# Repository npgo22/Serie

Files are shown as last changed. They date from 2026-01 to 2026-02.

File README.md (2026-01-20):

# Serie
Serie is a basic mainboard built to handle:
1. Insanely high temperatures
2. Insanely high speeds
3. Several axis of movement

The board itself is based around an STM32H723, the fastest microcontroller supported by Klipper at the moment.

## I/O
Currently, the following I/O is planned:

### Temperature sensing
Four MAX31856 (for type-k thermocouples) modules will be integrated for temperature sensing to be used as follows:
1. Hotend
2. Bed
3. Chamber
4. Spare/standby

Several other standard thermistor inputs will be broken out as needed.

### Motors
There will be 6x motors driven by TMC2241s. Each TMC2241 Support to klipper will need to be added to support this.

### Isolated Inputs
There are 16 digitally isolated inputs.

### Low Power Outputs
There are 6 outputs driven by small MOSFETs for outputs to other devices.

### Buses
As many buses should be broken out as possible.

### 12V Outputs
There are four 12V outputs to drive peripherals such as fans.

### USB
There will be at least 1 USB-C input.

### Ethernet
As I have ethernet stuff on hand, this board will have ethernet.

### Piezo Inputs
There will be a transimpedance amplifier followed by an instrumentation amplifier and an external comparator for piezo measurement. This is because the beacon probe cannot handle higher temperatures.

### Endstops
The enstops will utilize optoisolated inputs, and will be 3 pins to accomodate hall effect sensors.

## Power
As of right now, it is planned to require an external 48V power supply for the motors and a 12V power supply for the mainboard. This maintains galvanic isolation while providing decent protection against  A small switching regulator will generate 5V (AP62300TWU-7 + ETQP4M3R3KVK) which will then be fed into a 2112K-3.3.

### Heaters
Bed and chamber will be mains-powered, and motors will see 48V to 60V. and all the fans will maintain 12V, and the hotend heater cartridge will be able to handle 24V but will require a separate power supply just for it.

#### Switching
Mains powered items will be driven by an SSR, which necessitates the selection of a decent gate driver.

### Motors
Motors will be powered by a separate 48V power supply as they are extremely noisy.

## Board construction
Probably 4 layers. Don't really need more at this time.

## Misc.
* Consider a standardized header for breaking out to other boards.
* Total BoM cost for 2x is expected to be in the neighborhood of $150 once it's all assembled.

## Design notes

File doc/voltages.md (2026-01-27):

# Regulators
A set of voltage regulators can be seen on the regulators sheet. They are as follows:

|Regulator|Rail |Purpose|
|---|-----|---|
|AP64500  |+12V |For fans|
|AP64500  |+5V  |For digital +5V peripherals|
|AP2112K  |+3.3V|For low-power 3.3V peripherals|
|TPS7A2 |+4.5V|Specifically for the load cell|

For each of them, a set of 22uF capacitors are used in parallel to lower ESR/ESL and to raise the effective capcitance. The AP64500 uses frequency spread techniques to decrease noise among a few other tricks, which is important for our application. Ripple current is managed by the aforementioned 22uF capacitor sets. 

## AP64500 General
Generally, we do not use the UVLO feature as it adds complexity to the BOM and the case of a brownout doesn't really affect anything. Furthermore, a target switching frequency of 500 kHz is used as is standard to simplify math. This gives us the value for the RT/CLK pin of $200\mathrm{k\Omega}$.

We do not require power sequencing for this application, either, so we just tie EN to VIN.

### AP64500 Math
We already use $10\mathrm{k\Omega}$ resistors elsewhere in the design, so to calculate R1:

$$ R_1 = R_2 \cdot (\frac{V_{out}}{0.8\mathrm{V}} - 1) = 10,000\cdot(\frac{12\mathrm{V}}{0.8\mathrm{V}} - 1) = 140\mathrm{k\Omega}$$
$$ R_1 = R_2 \cdot (\frac{V_{out}}{0.8\mathrm{V}} - 1) = 10,000\cdot(\frac{5\mathrm{V}}{0.8\mathrm{V}} - 1) = 52.5\mathrm{k\Omega}$$

The closest E96 values for these are $140\mathrm{k\Omega}$ exact and $52.3\mathrm{k\Omega}$.

Now for the inductor at the top of our expected input voltage:
$$L = V_{out}\cdot\frac{(V_{in}-V_{out})}{V_{in}\cdot\Delta I_L \cdot f_{sw}} = \frac{12\mathrm{V}\cdot(24\mathrm{V}-12\mathrm{V})}{24\mathrm{V}\cdot2.5\mathrm{A}\cdot500,000} = 4.8\mathrm{\mu H}$$

$$L = V_{out}\cdot\frac{(V_{in}-V_{out})}{V_{in}\cdot\Delta I_L \cdot f_{sw}} = \frac{5\mathrm{V}\cdot(24\mathrm{V}-5\mathrm{V})}{24\mathrm{V}\cdot2.5\mathrm{A}\cdot500,000} = 3.167\mathrm{\mu H}$$

Now we should round up because a standard LED strip power supply can be cranked up in excess of the rated output voltage. As such, we will use inductor values of $6.8\mathrm{\mu H}$ and $3.3\mathrm{\mu H}$ far above our expected carrying current capacity of 5A, respectively.

Now before we go further we have to look at our deratings. For our application, the only reasonably-sized capacitors we can use at this point are 0805 X5R. X7R does not have the required voltage ratings. We will use the data from Samsung's [CL21A226MAYNNN](https://product.samsungsem.com/mlcc/CL21A226MAYNNN.do), which clearly shows a derating of -83% at 12V and -60% at 5V.

So we get:
$$3\cdot22\mathrm{\mu F}\cdot(1-0.83)=11.22\mathrm{\mu F}$$
$$3\cdot22\mathrm{\mu F}\cdot(1-0.6)=26.4\mathrm{\mu F}$$

From here we now need to calculate our values for External Loop Compensation (crossover frequency of $\frac{1}{10}f_{sw}$):

$$R_5=\frac{2\pi\cdot f_c \cdot V_{out} \cdot C_O \cdot R_T}{g_m\cdot V_{FB}}

=4.67\cdot10^3\cdot 50,000 \cdot 12\mathrm{V}\cdot 11.22\mathrm{\mu F} = 31.438\mathrm{k\Omega}$$
and:
$$R_5=\frac{2\pi\cdot f_c \cdot V_{out} \cdot C_O \cdot R_T}{g_m\cdot V_{FB}}

=4.67\cdot10^3\cdot 50,000 \cdot 5\mathrm{V}\cdot 26.4\mathrm{\mu F} = 30,822\mathrm{k\Omega}$$

The capacitor values were then both calculated to be 
$856\mathrm{pF} and 855\mathrm{pF}$, respectively.

This is actually a fairly fortunate coincidence that will allow for BOM consolidation:
Both resistors are going to be $30.9\mathrm{k\Omega}$ and $1\mathrm{nF}$.

Finally, we can calculate our expected output ripple:

$$V_{ripple} = \Delta I_L \cdot (\mathrm{ESR} + \frac{1}{8\cdot f_{sw} \cdot C_{OUT}}) $$

Which comes out to (assuming ESR is $0.67\mathrm{m\Omega}$ since it's $2\mathrm{m\Omega}$ for a single resistor) $40.4\mathrm{mV}$ for the +12V rail total and $22.7\mathrm{mV}$ for the +5V rail.

This is super low, and our only real concern is output transients causing the rail to sag, however this is irrelevant on both rails (+5V draws little current, +12V is just fans).

## LDOs
For both, we just used a handfull of input and output capacitors to minimize ripple. The LDOs used have really good high-frequency PSRRs, so we don't really worry about any sort of filtering past this. 

For USB power, only the main USB power is considered. This is just to simplify power plane management, and the scenarios wherein you would only have 1 USB port available are far and few between.

A diode is applied on the 5V regulator's output to prevent backflow when external USB power is supplied.

The +4.5V regulator was chosen in accordance with the minimum USB voltage of +4.8V minus the dropout.

### Expected ripple
From above we got the output ripple from our +5V regulator which feeds our LDOs. This came out to $22.7\mathrm{mV}$. If we estimate the PSRR (each eyeballed from the datasheets graphs) for the AP2112K to be 25dB and 55dB for the TPS7A20 at 500kHz, we can do some log math to derive the HF attenuation will be 17.8x for the AP2112K and 562x for the TPS7A20. This means our ripple is projected to be around 0.08mV and 1.65mV, respectively. These figures are more tha suitable for our purposes. With figures so good, it is meaningless to add more filtering, and in fact adding more will worsen performance as it will most certainly cause resonances.

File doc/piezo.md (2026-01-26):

# Piezo Circuit
This board integrates a simple charge amplifier followed by a discrete two-stage PGA followed by a comparator to achieve a fairly sensitive high-temperature piezo trigger circuit. We are aiming to measure down to 0.005N with a standard PZT-5A piezo as a stretch goal.

The circuit itself consists of a charge amplifier feeding into a noninverting discrete programmable gain amplifier followed by a voltage follower to prevent output loading. In addition, the last available opamp channel is used to generate a virtual ground.

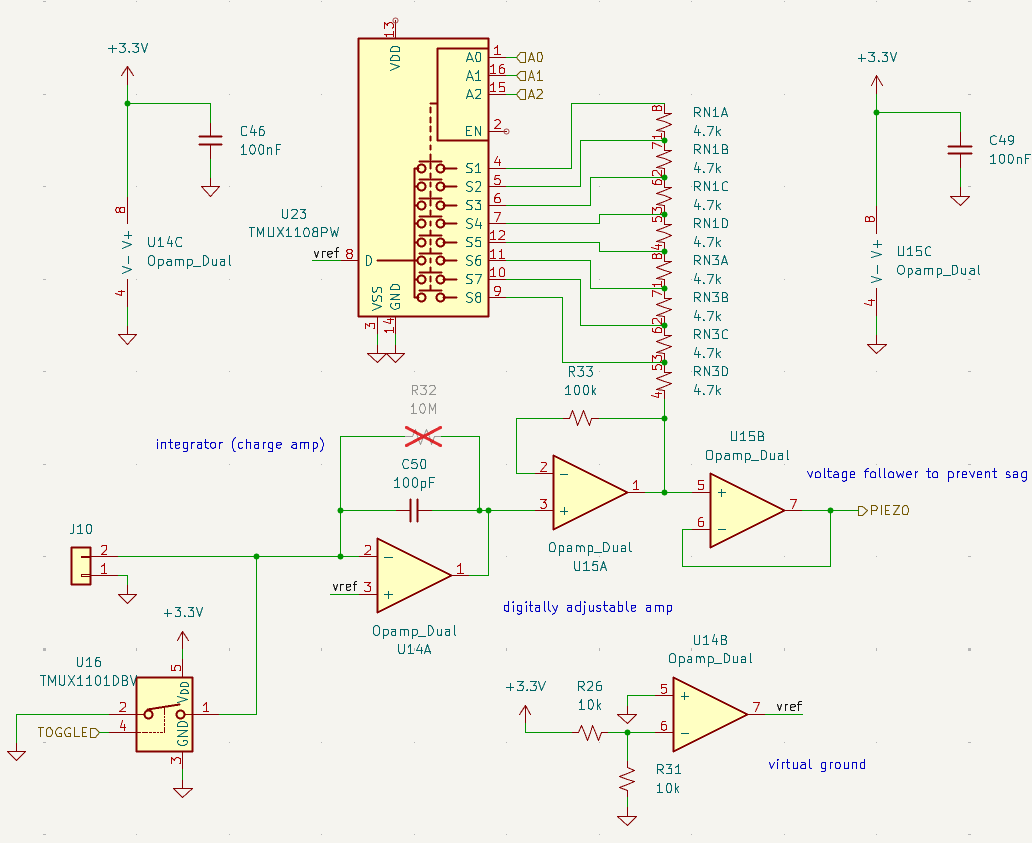
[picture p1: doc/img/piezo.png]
An incomplete picture of the piezo circuit Incomplete circuit


## Charge Amplifier
Here we needed the signal to be significant enough to not be consumed by noise. As a PZT-5A piezo has a $d_{33} = 390\cdot 10^{-12} \mathrm{\frac{C}{N}}$, we went with a capacitor value of ${100\mathrm{pF}}$ such that:
$$ V_{charge} = \frac{390\cdot10^{-12} \mathrm{\frac{C}{N}} \cdot 0.005\mathrm{N}}{100\cdot 10^{-12}} = 19.5\mathrm{mV}$$

At the top our range, this comes out to:
$$ V_{charge} = \frac{390\cdot10^{-12} \mathrm{\frac{C}{N}} \cdot 0.1\mathrm{N}}{100\cdot 10^{-12}} = 390\mathrm{mV}$$

Both of these values are very usable for our purposes.

## Non-Inverting Amplifier
The gain of a non-inverting amplifier is: $$G = 1+\frac{R_F}{R_2}$$
From this, we just plug in our values to achieve:
$$G = 1+\frac{100,000\Omega}{n\cdot4,700\Omega}$$
Where $n$ is the active amount of resistors in our resistor ladder as seen on the mux.
From this, we get the folowing table:
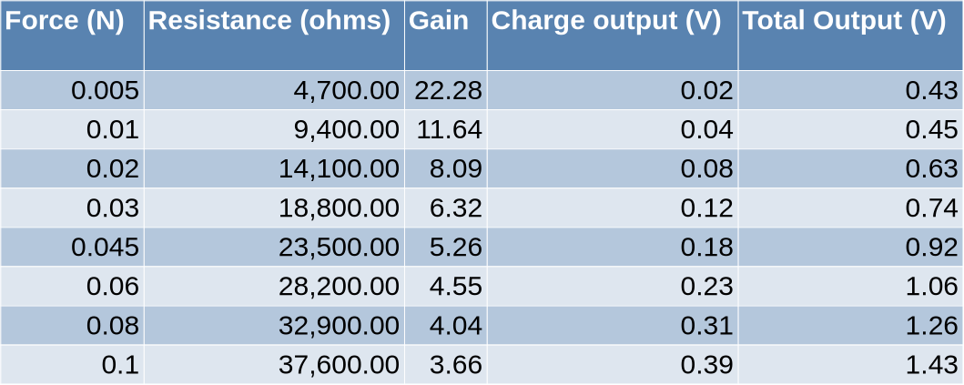
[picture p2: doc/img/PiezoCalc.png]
Piezo calculations Piezo Calculations


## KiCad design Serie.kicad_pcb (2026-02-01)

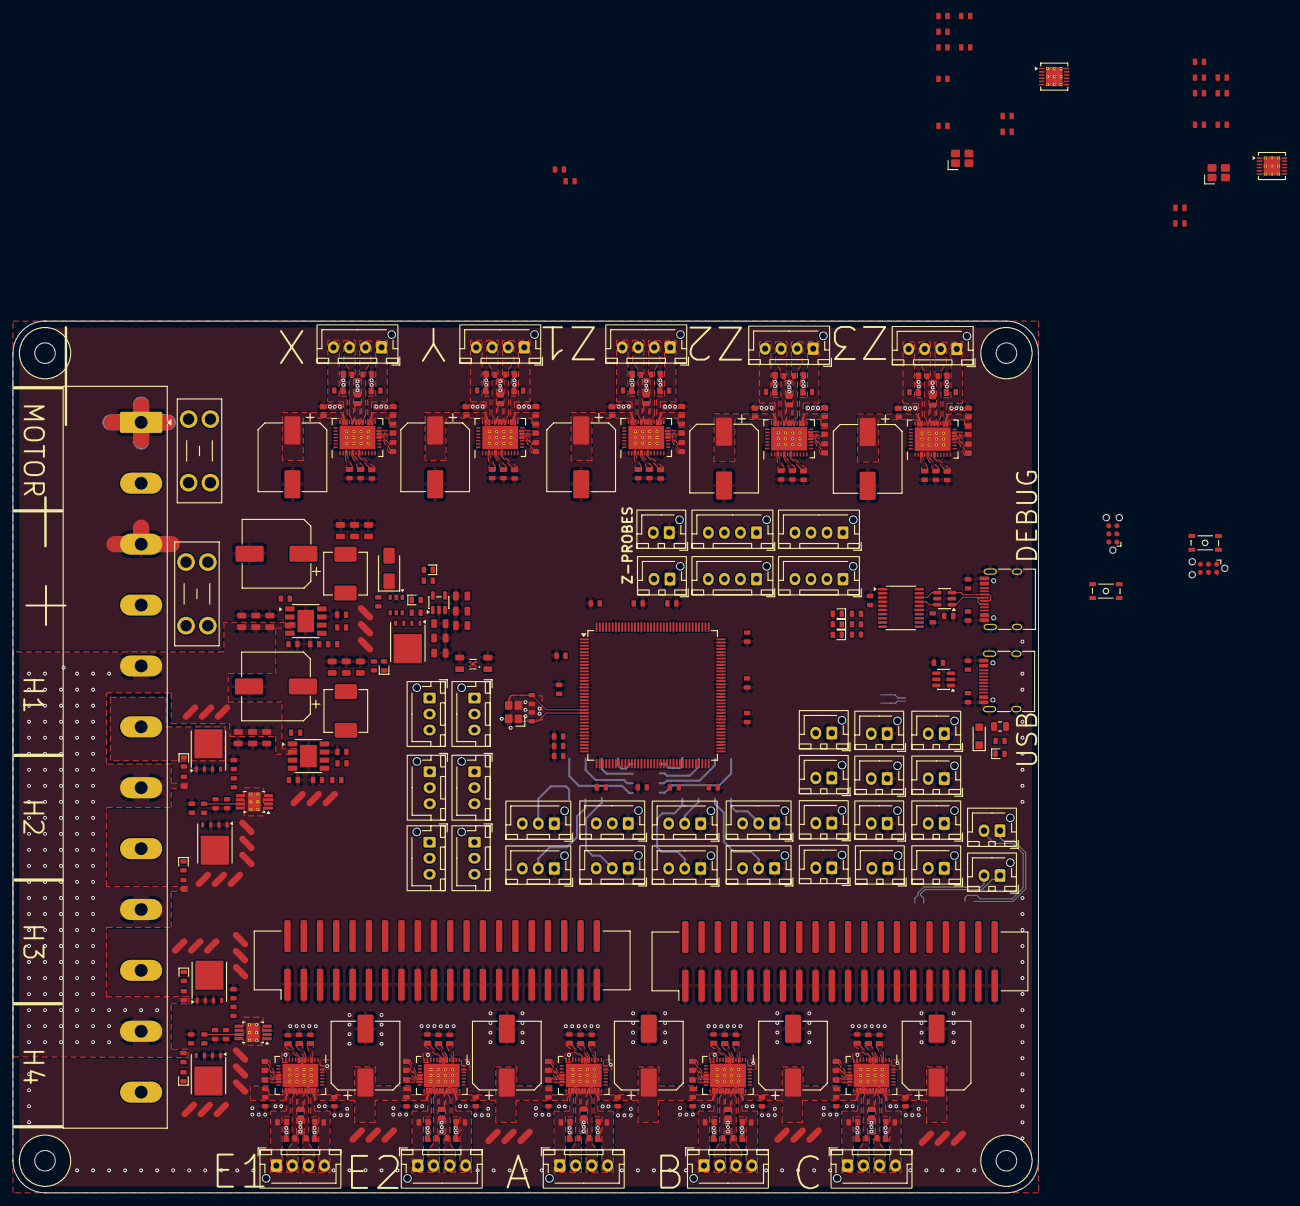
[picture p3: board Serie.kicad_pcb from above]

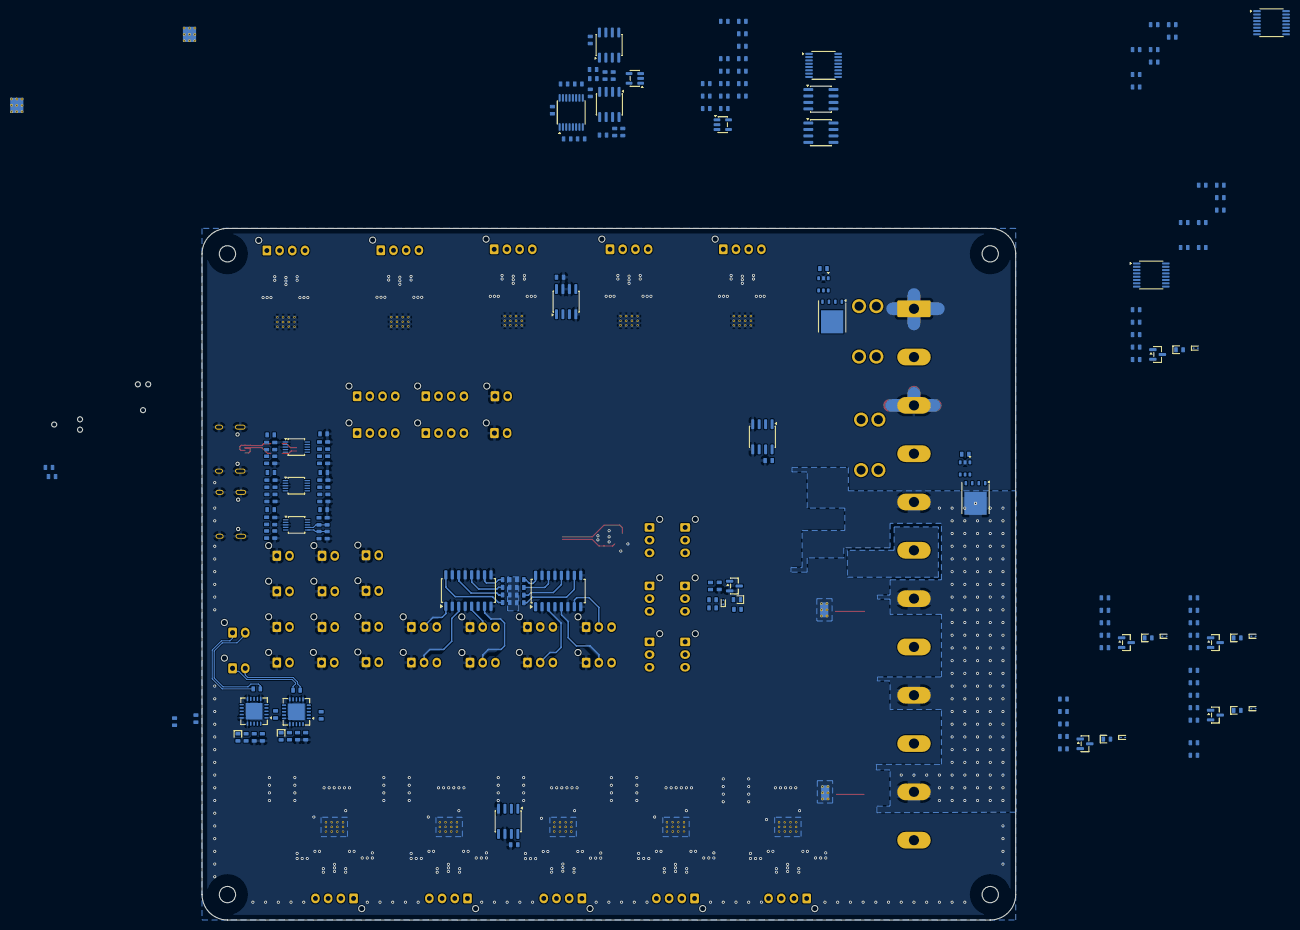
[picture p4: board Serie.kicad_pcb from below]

Board: 6 copper layers, 160.0 x 136.0 mm, 518 parts (179 on the bottom side), 303 nets.

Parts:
C1, C2: 10pF; C_0603
C3, C4, C93, C105, C117, C129, C141, C153, C184, C214, C226, C238: 2.2uF; C_0603
C5, C6, C7, C9, C12, C13, C14, C18, C19, C20, C21, C22, C24, C25, C26, C27, C28, C36, C38, C46, C56, C58, C59, C60, C61, C62, C63, C64, C65, C66, C67, C68, C69, C70, C71, C72, C74, C76, C77, C79, C80, C84, C85, C86, C92, C96, C97, C98, C104, C108, C109, C110, C116, C120, C121, C122, C128, C132, C133, C134, C140, C144, C145, C146, C152, C154, C155, C156, C158, C161, C162, C163, C167, C168, C169, C170, C171, C175, C176, C177, C183, C185, C186, C187, C188, C189, C191, C192, C193, C194, C195, C197, C198, C199, C200, C201, C205, C206, C207, C213, C217, C218, C219, C225, C229, C230, C231, C237: 100nF; C_0603
C8, C11, C78, C81, C157, C160: 10nF; C_0603
C10, C159: 10uF; C_0603
C15, C16, C164, C165: ?uF; C_0603
C17, C166: 100pF; C_0603
C23, C172: 30pF; C_0603
C29, C30, C31, C33, C34, C35, C39, C40, C41, C43, C44, C45, C48, C49, C50, C51, C52, C53, C54, C55: 22uF; C_0805
C32, C42, C87, C99, C111, C123, C135, C147, C178, C208, C220, C232: 100uF; CP_Elec_10x10.5
C37, C47: 1nF; C_0603
C57, C73, C75: 1uF; C_0603
C82, C83, C94, C95, C106, C107, C118, C119, C130, C131, C142, C143, C173, C174, C203, C204, C215, C216, C227, C228: 22nF; C_0603
C88, C89, C90, C91, C100, C101, C102, C103, C112, C113, C114, C115, C124, C125, C126, C127, C136, C137, C138, C139, C148, C149, C150, C151, C179, C180, C181, C182, C209, C210, C211, C212, C221, C222, C223, C224, C233, C234, C235, C236: 470pF; C_0603
C190, C196, C202: 100n; C_0603
D1: PMEG3010BER; Nexperia_CFP3_SOD-123W
D2, D3, D4, D5, D6, D8, D9, D10, D11, D12, D13, D14, D16, D18, D22, D24, D26: LED_Small; LED_0603
D7: SS54; D_SMA
D15, D17, D19, D23, D25, D27: ESD9B3.3ST5G; D_SOD-923
D20, D21: LED; LED_0603
F1: 500mA; Fuse_0805_2012Metric
F2, F3: XF-508P-B-B; Fuseholder_Blade_Mini_Keystone_3568
H1, H2, H3, H4: MountingHole; MountingHole_3.2mm_M3
J1, J2: Conn_02x20_Counter_Clockwise; IDC-Header_2x20_P2.54mm_Vertical_SMD
J3, J9: Conn_ARM_SWD_TagConnect_TC2030-NL; Tag-Connect_TC2030-IDC-NL_2x03_P1.27mm_Vertical
J4, J5, J24, J25, J26, J27, J28, J29, J30, J31, J33, J46, J47, J48: Conn_01x04; JST_XH_B4B-XH-AM_1x04_P2.50mm_Vertical
J6, J22, J23, J32, J34, J35, J36, J37, J38, J39, J40, J41, J42, J43, J44, J45: Conn_01x02; JST_XH_B2B-XH-AM_1x02_P2.50mm_Vertical
J7, J8: USB_C_Receptacle_USB2.0_16P; USB_C_Receptacle_HRO_TYPE-C-31-M-12
J10: Screw_Terminal_06x01x02; TerminalBlock_Ningbo-Kagnex_HB9500M_1x12_P9.5mm
J11, J12, J13, J14, J15, J16, J17, J18, J19, J20, J21, J49, J50, J51: Conn_01x03; JST_XH_B3B-XH-AM_1x03_P2.50mm_Vertical
L1: 6.8 uH; L_Changjiang_FXL0630
L2: 3.3 uH; L_Changjiang_FXL0630
Q1, Q2, Q3, Q4, Q5, Q6, Q7: BSC016N06NS; TDSON-8-1
Q8, Q9, Q10, Q11, Q12, Q13: AO3400A; SOT-23
R1, R2, R81, R82: 100R; R_0603
R3, R4, R5, R6, R7, R8, R9, R10, R16, R17, R21, R22, R48, R53, R58, R83, R84, R85, R86, R87, R88, R89, R90, R96, R97, R98, R99, R103, R104, R105, R106, R108, R109, R110, R111, R118, R123, R128: 4.7k; R_0603
R11, R36, R39, R42, R45, R50, R55, R60, R91, R120, R125, R130: 100k; R_0603
R12, R92: 10M; R_0603
R13, R14, R15, R18, R19, R20, R23, R25, R28, R31, R33, R34, R37, R40, R43, R46, R47, R51, R52, R56, R57, R61, R62, R63, R64, R65, R66, R67, R68, R69, R70, R72, R73, R93, R94, R100, R101, R102, R107, R112, R116, R117, R121, R122, R126, R127: 10k; R_0603
R24: 140k; R_0603
R26, R30: 200k; R_0603
R27, R32: 30.9k; R_0603
R29: 52.5k; R_0603
R35, R38, R41, R44, R49, R54, R59, R119, R124, R129: 10R; R_0603
R71, R74: 4.02k; R_0603
R75, R76, R77, R78, R79, R80, R95, R113, R114, R115: 24k; R_0603
SW1, SW2: SKRPANE010
U1: STM32H723ZGT6; LQFP-144_20x20mm_P0.5mm
U2, U30: ADS1220xPW; TSSOP-16_4.4x5mm_P0.65mm
U3, U31: TMUX1108PW; TSSOP-16_4.4x5mm_P0.65mm
U4, U5, U32, U33: TLV6742; SOIC-8_3.9x4.9mm_P1.27mm
U6, U34: LDC1612; WSON-12-1EP_4x4mm_P0.5mm_EP2.6x3mm_ThermalVias
U7, U35: TMUX1101DBV; SOT-23-5
U8, U10: USBLC6-2SC6; SOT-23-6
U9: STM32F042F4Px; TSSOP-20_4.4x6.5mm_P0.65mm
U11, U13: AP64500; Diodes_SO-8EP
U12, U14, U17: AP74700Q; SOT-6
U15: TLV77533; SOT-23-5
U16: TPS7A20xxxDQN; Texas_X2SON-4_1x1mm_P0.65mm
U18, U19: UCC27524DGN; Texas_DGN0008G_VSSOP-8-1EP_3x3mm_P0.65mm_EP2x2.94mm_Mask1.8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
U20, U21: LTV-247; SOP-16_4.4x10.4mm_P1.27mm
U22, U23: MAX31865xTP; TQFN-20-1EP_5x5mm_P0.65mm_EP3.25x3.25mm
U24, U25, U26, U27, U28, U29, U36, U43, U44, U45: TMC2241ATC; QFN-38_EP_5.63x7.6_Pitch0.5mm
U37, U39, U42: ADS1115IDGS; TSSOP-10_3x3mm_P0.5mm
U38, U40, U41: LM75B; SOIC-8_3.9x4.9mm_P1.27mm
Y1: 25 MHz; 3225-4P-L
Y2, Y3: 12 MHz; 3225-4P-L

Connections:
+3.3V: C5.2, C7.2, C12.2, C13.2, C14.1, C22.1, C24.1, C25.1, C51.2, C52.2, C53.2, C57.2, C58.2, C59.2, C60.2, C61.2, C62.2, C63.2, C64.2, C65.2, C66.2, C67.2, C68.2, C69.2, C70.2, C71.2, C76.1, C77.1, C79.1, C80.1, C92.2, C104.2, C116.2, C128.2, C140.2, C152.2, C154.2, C156.2, C161.2, C162.2, C163.1, C171.1, C183.2, C185.1, C186.1, C191.1, C192.1, C197.1, C198.1, C213.2, C225.2, C237.2, D3.2 (A), D4.2 (A), D5.2 (A), J3.1 (VCC), J9.1 (VCC), J14.3, J15.3, J16.3, J17.3, J18.3, J19.3, J20.3, J21.3, R13.1, R33.1, R46.1, R51.1, R56.1, R61.1, R62.1, R63.1, R64.1, R65.1, R66.1, R67.1, R68.1, R69.1, R70.1, R72.1, R73.1, R93.1, R96.1, R97.1, R98.1, R99.1, R100.2, R101.2, R102.2, R103.1, R104.1, R105.1, R106.1, R107.2, R108.1, R109.1, R110.1, R111.1, R112.2, R116.1, R121.1, R126.1, U1.6 (VBAT), U1.17 (VDD), U1.30 (VDD), U1.32 (VREF+), U1.33 (VDDA), U1.39 (VDD), U1.52 (VDD), U1.62 (VDD), U1.72 (VDD), U1.84 (VDD), U1.95 (VDD33USB), U1.108 (VDD), U1.121 (VDD), U1.131 (VDD), U1.143 (PDR_ON), U1.144 (VDD), U2.13 (DVDD), U3.2 (EN), U3.13 (VDD), U4.8 (V+), U5.8 (V+), U6.7 (VDD), U7.5 (V_{DD}), U9.5 (VDDA), U9.16 (VDD), U15.5 (VOUT), U22.19 (DVDD), U22.20 (VDD), U23.19 (DVDD), U23.20 (VDD), U24.7 (VCCIO), U24.33 (~SLEEP), U25.7 (VCCIO), U25.33 (~SLEEP), U26.7 (VCCIO), U26.33 (~SLEEP), U27.7 (VCCIO), U27.33 (~SLEEP), U28.7 (VCCIO), U28.33 (~SLEEP), U29.7 (VCCIO), U29.33 (~SLEEP), U30.13 (DVDD), U31.2 (EN), U31.13 (VDD), U32.8 (V+), U33.8 (V+), U34.7 (VDD), U35.5 (V_{DD}), U36.7 (VCCIO), U36.33 (~SLEEP), U37.8 (VDD), U38.6 (A1), U38.7 (A0), U38.8 (+Vs), U39.1 (ADDR), U39.8 (VDD), U40.5 (A2), U40.8 (+Vs), U41.5 (A2), U41.7 (A0), U41.8 (+Vs), U42.8 (VDD), U43.7 (VCCIO), U43.33 (~SLEEP), U44.7 (VCCIO), U44.33 (~SLEEP), U45.7 (VCCIO), U45.33 (~SLEEP), Y2.4 (V+), Y3.4 (V+)
+4.5V: C6.1, C10.1, C55.1, C155.1, C159.1, J4.4, J30.4, U2.11 (AIN0/REFP1), U2.12 (AVDD), U16.1 (OUT), U30.11 (AIN0/REFP1), U30.12 (AVDD)
+5V: C48.2, C49.2, C50.2, C54.1, D1.1 (K), Q2.5 (D), U14.4 (CATHODE), U15.1 (VIN), U15.3 (EN), U16.3 (EN), U16.4 (IN)
+12V: C32.1, C33.1, C34.1, C35.1, C72.2, C73.2, C74.2, C75.2, J11.1, J12.1, J13.1, J49.1, J50.1, J51.1, L1.2, R23.1, R24.1, R47.1, R52.1, R57.1, R117.1, R122.1, R127.1, U18.1 (ENA), U18.6 (V_{DD}), U18.8 (ENB), U19.1 (ENA), U19.6 (V_{DD}), U19.8 (ENB)
+24V: C29.1, C30.1, C31.1, C39.1, C40.1, C41.1, J10.5 (Pin_1), J10.7 (Pin_1), J10.9 (Pin_1), J10.11 (Pin_1), Q1.5 (D), R34.1, R37.1, R40.1, R43.1, U11.2 (VIN), U11.3 (EN), U12.4 (CATHODE), U13.2 (VIN), U13.3 (EN)
/Connections/Debugger and USB/IF_SWCLK: J9.4 (SWCLK), U9.20 (PA14)
/Connections/Debugger and USB/IF_SWDIO: J9.2 (SWDIO), U9.19 (PA13)
/Connections/Debugger and USB/USB_CONN_D+: J7.A6 (D+), J7.B6 (D+), J8.A6 (D+), J8.B6 (D+), U8.3 (I/O2), U10.3 (I/O2)
/Connections/Debugger and USB/USB_CONN_D-: J7.A7 (D-), J7.B7 (D-), J8.A7 (D-), J8.B7 (D-), U8.1 (I/O1), U10.1 (I/O1)
/Connections/Debugger and USB/USB_D+: U9.18 (PA10/PA12), U10.4 (I/O2)
/Connections/Debugger and USB/USB_D-: U9.17 (PA9/PA11), U10.6 (I/O1)
/Connections/Debugger and USB/~RST: J9.3 (~RESET), SW2.3 (K), SW2.4 (A), U9.4 (NRST)
/Connections/High Power Outputs 1/OUTA: R35.1, U18.5 (OUTB)
/Connections/High Power Outputs 1/OUTB: R38.1, U18.7 (OUTA)
/Connections/High Power Outputs 2/OUTA: R41.1, U19.5 (OUTB)
/Connections/High Power Outputs 2/OUTB: R44.1, U19.7 (OUTA)
/Connections/IN1: R61.2, U20.16
/Connections/IN2: R62.2, U20.14
/Connections/IN3: R63.2, U20.12
/Connections/IN4: R64.2, U20.10
/Connections/IN5: R65.2, U21.16
/Connections/IN6: R66.2, U21.14
/Connections/IN7: R67.2, U21.12
/Connections/IN8: R68.2, U21.10
/Connections/Low Power Outputs/TACH1: D15.2 (A2), R46.2, R48.2
/Connections/Low Power Outputs/TACH2: D17.2 (A2), R51.2, R53.2
/Connections/Low Power Outputs/TACH3: D19.2 (A2), R56.2, R58.2
/Connections/Low Power Outputs/TACH4: D23.2 (A2), R116.2, R118.2
/Connections/Low Power Outputs/TACH5: D25.2 (A2), R121.2, R123.2
/Connections/Low Power Outputs/TACH6: D27.2 (A2), R126.2, R128.2
/Connections/SWCLK: J3.4 (SWCLK), U1.109 (PA14(JTCK), U9.12 (PA6)
/Connections/SWDIO: J3.2 (SWDIO), U1.105 (PA13(JTMS), U9.11 (PA5)
/Connections/Sensors 1/CLK: C23.1, U6.3 (CLKIN), Y2.3 (OUT)
/Connections/Sensors 1/PIEZO: U5.6 (-), U5.7
/Connections/Sensors 1/vref: U3.8 (D), U4.3 (+), U4.7
/Connections/Sensors 2/CLK: C172.1, U34.3 (CLKIN), Y3.3 (OUT)
/Connections/Sensors 2/PIEZO: U33.6 (-), U33.7
/Connections/Sensors 2/vref: U31.8 (D), U32.3 (+), U32.7
/Connections/Thermistors/SCL: R101.1, U37.10 (SCL), U38.2 (SCL), U39.10 (SCL), U40.2 (SCL), U41.2 (SCL), U42.10 (SCL)
/Connections/Thermistors/SDA: R102.1, U37.9 (SDA), U38.1 (SDA), U39.9 (SDA), U40.1 (SDA), U41.1 (SDA), U42.1 (ADDR), U42.9 (SDA)
/Connections/Thermistors/TS_ALRT/RDY_1: R100.1, U37.2 (ALERT/RDY)
/Connections/Thermistors/TS_ALRT/RDY_2: R107.1, U39.2 (ALERT/RDY)
/Connections/Thermistors/TS_ALRT/RDY_3: R112.1, U42.2 (ALERT/RDY)
/Connections/Thermocouple 1/T1+: C78.1, J22.2, U22.5 (FORCE+), U22.7 (RTDIN+)
/Connections/Thermocouple 1/T1-: C78.2, J22.1, U22.8 (RTDIN-), U22.9 (FORCE-)
/Connections/Thermocouple 2/T1+: C81.1, J23.2, U23.5 (FORCE+), U23.7 (RTDIN+)
/Connections/Thermocouple 2/T1-: C81.2, J23.1, U23.8 (RTDIN-), U23.9 (FORCE-)
/Connections/~RST: J3.3 (~RESET), SW1.1, SW1.2, U1.25 (NRST), U9.14 (PB1)
/Connections/~TC_CS_1: R70.2, U22.13 (~CS)
/Connections/~TC_CS_2: R73.2, U23.13 (~CS)
DRV_MISO: U24.37 (SDO/NAO), U25.37 (SDO/NAO), U26.37 (SDO/NAO), U27.37 (SDO/NAO), U28.37 (SDO/NAO), U29.37 (SDO/NAO), U36.37 (SDO/NAO), U43.37 (SDO/NAO), U44.37 (SDO/NAO), U45.37 (SDO/NAO)
DRV_MOSI: U24.36 (SDI/AD0), U25.36 (SDI/AD0), U26.36 (SDI/AD0), U27.36 (SDI/AD0), U28.36 (SDI/AD0), U29.36 (SDI/AD0), U36.36 (SDI/AD0), U43.36 (SDI/AD0), U44.36 (SDI/AD0), U45.36 (SDI/AD0)
DRV_SCK: U24.35 (SCK/AD1), U25.35 (SCK/AD1), U26.35 (SCK/AD1), U27.35 (SCK/AD1), U28.35 (SCK/AD1), U29.35 (SCK/AD1), U36.35 (SCK/AD1), U43.35 (SCK/AD1), U44.35 (SCK/AD1), U45.35 (SCK/AD1)
GND: C1.1, C2.1, C3.1, C4.1, C5.1, C6.2, C7.1, C8.1, C11.2, C12.1, C13.1, C14.2, C18.1, C19.1, C20.1, C21.1, C22.2, C23.2, C24.2, C25.2, C26.2, C27.2, C29.2, C30.2, C31.2, C32.2, C33.2, C34.2, C35.2, C37.2, C39.2, C40.2, C41.2, C42.2, C43.2, C44.2, C45.2, C47.2, C48.1, C49.1, C50.1, C51.1, C52.1, C53.1, C54.2, C55.2, C57.1, C58.1, C59.1, C60.1, C61.1, C62.1, C63.1, C64.1, C65.1, C66.1, C67.1, C68.1, C69.1, C70.1, C71.1, C72.1, C73.1, C74.1, C75.1, C76.2, C77.2, C79.2, C80.2, C84.2, C85.2, C86.2, C87.2, C88.2, C89.2, C90.2, C91.2, C92.1, C93.1, C96.2, C97.2, C98.2, C99.2, C100.2, C101.2, C102.2, C103.2, C104.1, C105.1, C108.2, C109.2, C110.2, C111.2, C112.2, C113.2, C114.2, C115.2, C116.1, C117.1, C120.2, C121.2, C122.2, C123.2, C124.2, C125.2, C126.2, C127.2, C128.1, C129.1, C132.2, C133.2, C134.2, C135.2, C136.2, C137.2, C138.2, C139.2, C140.1, C141.1, C144.2, C145.2, C146.2, C147.2, C148.2, C149.2, C150.2, C151.2, C152.1, C153.1, C154.1, C155.2, C156.1, C157.1, C160.2, C161.1, C162.1, C163.2, C167.1, C168.1, C169.1, C170.1, C171.2, C172.2, C175.2, C176.2, C177.2, C178.2, C179.2, C180.2, C181.2, C182.2, C183.1, C184.1, C185.2, C186.2, C187.1, C188.1, C189.1, C190.1, C191.2, C192.2, C193.1, C194.1, C195.1, C196.1, C197.2, C198.2, C199.1, C200.1, C201.1, C202.1, C205.2, C206.2, C207.2, C208.2, C209.2, C210.2, C211.2, C212.2, C213.1, C214.1, C217.2, C218.2, C219.2, C220.2, C221.2, C222.2, C223.2, C224.2, C225.1, C226.1, C229.2, C230.2, C231.2, C232.2, C233.2, C234.2, C235.2, C236.2, C237.1, C238.1, D2.1 (K), D6.1 (K), D8.1 (K), D9.1 (K), D15.1 (A1), D17.1 (A1), D19.1 (A1), D23.1 (A1), D25.1 (A1), D27.1 (A1), J1.1, J1.3, J1.5, J1.7, J1.9, J1.11, J1.13, J1.15, J1.17, J1.19, J1.21, J1.23, J1.25, J1.27, J1.29, J1.31, J1.33, J1.35, J1.37, J1.39, J2.1, J2.3, J2.5, J2.7, J2.9, J2.11, J2.13, J2.15, J2.17, J2.19, J2.21, J2.23, J2.25, J2.27, J2.29, J2.31, J2.33, J2.35, J2.37, J2.39, J3.5 (GND), J6.1, J7.A1 (GND), J7.A12 (GND), J7.B1 (GND), J7.B12 (GND), J7.S1 (SHIELD), J8.A1 (GND), J8.A12 (GND), J8.B1 (GND), J8.B12 (GND), J8.S1 (SHIELD), J9.5 (GND), J10.1, J10.3 (Pin_1), J14.1, J15.1, J16.1, J17.1, J18.1, J19.1, J20.1, J21.1, J32.1, J34.1, J35.1, J36.1, J37.1, J38.1, J39.1, J40.1, J41.1, J42.1, J43.1, J44.1, J45.1, Q4.1 (S), Q4.2 (S), Q4.3 (S), Q5.1 (S), Q5.2 (S), Q5.3 (S), Q6.1 (S), Q6.2 (S), Q6.3 (S), Q7.1 (S), Q7.2 (S), Q7.3 (S), Q8.2 (S), Q9.2 (S), Q10.2 (S), Q11.2 (S), Q12.2 (S), Q13.2 (S), R14.1, R16.1, R17.2, R21.1, R22.2, R25.2, R26.2, R30.2, R31.2, R36.1, R39.1, R42.1, R45.1, R50.1, R55.1, R60.1, R75.2, R76.2, R77.2, R78.2, R79.2, R80.2, R94.1, R95.2, R113.2, R114.2, R115.2, R120.1, R125.1, R130.1, SW1.3 (K), SW1.4 (A), SW2.1, SW2.2, U1.16 (VSS), U1.31 (VSSA), U1.38 (VSS), U1.51 (VSS), U1.61 (VSS), U1.83 (VSS), U1.94 (VSS), U1.107 (VSS), U1.120 (VSS), U1.130 (VSS), U1.138 (BOOT0), U2.3 (CLK), U2.4 (DGND), U2.5 (AVSS), U3.3 (VSS), U3.14 (GND), U4.4 (V-), U4.5 (+), U5.4 (V-), U6.4 (ADDR), U6.6 (SD), U6.8 (GND), U6.13 (GND), U7.2, U7.3 (GND), U8.2 (GND), U9.1 (PB8), U9.15 (VSSA), U10.2 (GND), U11.7 (GND), U11.9 (EP), U12.2 (GND), U13.7 (GND), U13.9 (EP), U14.2 (GND), U15.2 (GND), U16.2 (GND), U16.5 (Pad), U17.2 (GND), U18.3 (GND), U18.9 (GND), U19.3 (GND), U19.9 (GND), U20.2, U20.4, U20.6, U20.8, U20.9, U20.11, U20.13, U20.15, U21.2, U21.4, U21.6, U21.8, U21.9, U21.11, U21.13, U21.15, U22.6 (FORCE2), U22.10 (GND), U22.15 (DGND), U22.16 (GND), U22.21 (GND), U23.6 (FORCE2), U23.10 (GND), U23.15 (DGND), U23.16 (GND), U23.21 (GND), U24.6 (AGND), U24.11 (DRV_EN), U24.23 (PGND), U24.28 (PGND), U24.38 (CLK), U24.39 (EP), U25.6 (AGND), U25.11 (DRV_EN), U25.23 (PGND), U25.28 (PGND), U25.38 (CLK), U25.39 (EP), U26.6 (AGND), U26.11 (DRV_EN), U26.23 (PGND), U26.28 (PGND), U26.38 (CLK), U26.39 (EP), U27.6 (AGND), U27.11 (DRV_EN), U27.23 (PGND), U27.28 (PGND), U27.38 (CLK), U27.39 (EP), U28.6 (AGND), U28.11 (DRV_EN), U28.23 (PGND), U28.28 (PGND), U28.38 (CLK), U28.39 (EP), U29.6 (AGND), U29.11 (DRV_EN), U29.23 (PGND), U29.28 (PGND), U29.38 (CLK), U29.39 (EP), U30.3 (CLK), U30.4 (DGND), U30.5 (AVSS), U31.3 (VSS), U31.14 (GND), U32.4 (V-), U32.5 (+), U33.4 (V-), U34.4 (ADDR), U34.6 (SD), U34.8 (GND), U34.13 (GND), U35.2, U35.3 (GND), U36.6 (AGND), U36.11 (DRV_EN), U36.23 (PGND), U36.28 (PGND), U36.38 (CLK), U36.39 (EP), U37.1 (ADDR), U37.3 (GND), U38.4 (GND), U38.5 (A2), U39.3 (GND), U40.4 (GND), U40.6 (A1), U40.7 (A0), U41.4 (GND), U41.6 (A1), U42.3 (GND), U43.6 (AGND), U43.11 (DRV_EN), U43.23 (PGND), U43.28 (PGND), U43.38 (CLK), U43.39 (EP), U44.6 (AGND), U44.11 (DRV_EN), U44.23 (PGND), U44.28 (PGND), U44.38 (CLK), U44.39 (EP), U45.6 (AGND), U45.11 (DRV_EN), U45.23 (PGND), U45.28 (PGND), U45.38 (CLK), U45.39 (EP), Y1.2 (G), Y1.4 (G), Y2.2 (GND), Y3.2 (GND)
MCU_USB_D+: U1.104 (PA12), U8.4 (I/O2)
MCU_USB_D-: U1.103 (PA11), U8.6 (I/O1)
unnamed: C3.2, U1.71 (VCAP)
unnamed: C4.2, U1.106 (VCAP)
unnamed: C37.1, R27.2
unnamed: C47.1, R32.2
unnamed: D1.2 (A), F1.2, R15.1
unnamed: D2.2 (A), R15.2
unnamed: D3.1 (K), R18.1
unnamed: D4.1 (K), R19.1
unnamed: D5.1 (K), R20.1
unnamed: D6.2 (A), R23.2
unnamed: C42.1, C43.1, C44.1, C45.1, D7.2 (A), L2.2
unnamed: C46.2, D7.1 (K), Q2.1 (S), Q2.2 (S), Q2.3 (S), R28.1, R29.1, U14.3 (EN), U14.6 (ANODE)
unnamed: D8.2 (A), R28.2
unnamed: D9.2 (A), R33.2
unnamed: D10.2 (A), R34.2
unnamed: D10.1 (K), J10.6 (Pin_2), Q4.5 (D)
unnamed: D11.2 (A), R37.2
unnamed: D11.1 (K), J10.8 (Pin_2), Q5.5 (D)
unnamed: D12.2 (A), R40.2
unnamed: D12.1 (K), J10.10 (Pin_2), Q6.5 (D)
unnamed: D13.2 (A), R43.2
unnamed: D13.1 (K), J10.12 (Pin_2), Q7.5 (D)
unnamed: D14.2 (A), R47.2
unnamed: D14.1 (K), J11.2, Q8.3 (D)
unnamed: D16.2 (A), R52.2
unnamed: D16.1 (K), J12.2, Q9.3 (D)
unnamed: D18.2 (A), R57.2
unnamed: D18.1 (K), J13.2, Q10.3 (D)
unnamed: D20.2 (A), R69.2
unnamed: D20.1 (K), U22.18 (~DRDY)
unnamed: D21.2 (A), R72.2
unnamed: D21.1 (K), U23.18 (~DRDY)
unnamed: D22.2 (A), R117.2
unnamed: D22.1 (K), J49.2, Q11.3 (D)
unnamed: D24.2 (A), R122.2
unnamed: D24.1 (K), J50.2, Q12.3 (D)
unnamed: D26.2 (A), R127.2
unnamed: D26.1 (K), J51.2, Q13.3 (D)
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

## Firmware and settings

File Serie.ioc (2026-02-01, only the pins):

Mcu.UserName=STM32H723ZGTx
PA0.Signal=UART4_TX
PA1.Signal=UART4_RX
PA11.Signal=USB_OTG_HS_DM
PA12.Signal=USB_OTG_HS_DP
PA5.Signal=SPI6_SCK
PA6.Signal=SPI6_MISO
PA7.Signal=SPI6_MOSI
PA8.Signal=I2C3_SCL
PB0.GPIO_Label=MOTOR6_DIR
PB0.Signal=GPIO_Output
PB1.GPIO_Label=MOTOR6_DIAG
PB1.Signal=GPIO_Input
PB10.Signal=I2C2_SCL
PB11.Signal=I2C2_SDA
PB13.Signal=SPI2_SCK
PB14.Signal=SPI2_MISO
PB15.Signal=SPI2_MOSI
PB3(JTDO/TRACESWO).Signal=SPI3_SCK
PB4(NJTRST).Signal=SPI3_MISO
PB5.Signal=SPI3_MOSI
PB6.Signal=GPIO_Output
PB7.Signal=GPIO_Output
PB8.Signal=GPIO_Output
PB9.Signal=GPIO_Output
PC11.Signal=GPIO_Output
PC12.Signal=GPIO_Output
PC13.Signal=GPIO_Output
PC14-OSC32_IN.Signal=GPIO_Output
PC15-OSC32_OUT.Signal=GPIO_Output
PC4.GPIO_Label=MOTOR6_CS
PC4.Signal=GPIO_Output
PC5.GPIO_Label=MOTOR6_STEP
PC5.Signal=GPIO_Output
PC9.Signal=I2C3_SDA
PD0.Signal=GPIO_Output
PD1.Signal=GPIO_Output
PD2.Signal=GPIO_Output
PD3.Signal=GPIO_Output
PD4.Signal=GPIO_Output
PD7.Signal=SPI1_MOSI
PE0.Signal=GPIO_Output
PE1.Signal=GPIO_Output
PE12.Signal=SPI4_SCK
PE13.Signal=SPI4_MISO
PE14.Signal=SPI4_MOSI
PE2.Signal=GPIO_Output
PE3.Signal=GPIO_Output
PE4.Signal=GPIO_Output
PE5.Signal=GPIO_Output
PE6.Signal=GPIO_Output
PE7.Signal=UART7_RX
PE8.Signal=UART7_TX
PF0.Signal=GPIO_Output
PF1.Signal=GPIO_Output
PF14.Signal=I2C4_SCL
PF15.Signal=I2C4_SDA
PF7.Signal=SPI5_SCK
PF8.Signal=SPI5_MISO
PF9.Signal=SPI5_MOSI
PG0.Signal=UART9_RX
PG1.Signal=UART9_TX
PG10.Signal=GPIO_Output
PG11.Signal=SPI1_SCK
PG12.Signal=GPIO_Output
PG13.Signal=GPIO_Output
PG14.Signal=GPIO_Output
PG15.Signal=GPIO_Output
PG9.Signal=SPI1_MISO

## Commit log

2026-01-14 Play around with drivers
    [Serie.kicad_pcb, drivers1.kicad_sch]
2026-01-17 I dont know whats going on here
    [Serie.kicad_sch, chagenotes.kicad_sch, connections.kicad_sch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]
2026-01-20 Soften scope, begin layout, reorganize sheets (still need to delete extras)
    [Serie.csv, Serie.kicad_pcb, chagenotes.kicad_sch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]
2026-01-27 Regulator decisions
2026-01-27 loadcell math coming soon(tm)
    [Serie.csv, Serie.kicad_pcb, chagenotes.kicad_sch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]
